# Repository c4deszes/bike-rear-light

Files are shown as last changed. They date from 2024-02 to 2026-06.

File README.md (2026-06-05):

# Rear Light

> An integrated tail, brake and turn signal light for bicycles.

## Gen 1

This generation is meant to demonstrate the tail light and brake light capabilities, turn signals
are not present.

The expected takeaways from it are:

- whether this simplified single PCB assembly is robust enough
- whether the amount of light produced is sufficient
- how certain lenses affect the optical qualities 
- what the thermals look like given the power consumption and enclosure with passive cooling
- whether this accelerometer is reliable to be used for the brake lights

Key findings:

- Accelerometer alone is not reliable for brake detection due to road vibrations. With filtering
  the reaction time goes up.
- Linear LED drivers are not efficient for the expected bus voltages, this is a problem for the
  continously on tail light
- Single LEDs spread out on a large area need lots of diffusing which reduces the light output

## Gen 1b

This generation is meant as a patch for the weak and uneven light output of Gen1. It's based on the
Gen1 front light hardware put inside a custom case.

There are no expectations.

Key findings:

- Mounting bracket broke during two incidents in an unservicable way

## Gen 2

This generation is meant to merge the good parts of Gen1 and Gen1b and improve a couple of things.
The main new feature is the included radar and the primary improvements are increased operational
voltage range and additional monitoring.

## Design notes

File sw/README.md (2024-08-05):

# Rear light software

## Open issues

- Scheduling automatic light diagnostic runs
- Fixing brake light error scenario determination
- Microcontroller temperature measurement and derating
- Accelerometer data processing and internal brake signal
- Diagnostic op. status and power status responses

## Deferred tasks

- Externally configurable product parameters (depends on diagnostic protocol extension)

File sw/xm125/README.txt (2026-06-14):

This package contains example source code, a makefile based build system, libraries, pre-built
binaries and documentation in order to start developing your own A121 radar applications
for the xm125 module.

Please see 'doc/XM125 Software User Guide.pdf' in order to get started with application development.

For more documentation please visit https://docs.acconeer.com/ or https://developer.acconeer.com

To view release notes use the following link: https://developer.acconeer.com/home/a121-docs-software/a121-sw-release-notes/

export GNU_INSTALL_ROOT=/opt/armgcc/arm-gnu-toolchain-14.2.rel1-x86_64-arm-none-eabi/bin/
export STM32CUBE_FW_L4_ROOT=/workspaces/xm125/STM32CubeL4/

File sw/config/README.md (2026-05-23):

# Board configurations

This folder includes board configurations for all released hardware versions.

Each board configuration must define the `bsp-config` interface target.
The target must have the following properties:
- Include folder
- BSP_IMU_DRIVER, defines the IMU driver to be used
- BSP_LED_DRIVER, defines the LED driver to be used

## IMU driver

Board configs currently can use `NONE` or `BMA456`. Whether the sensor is actually present is up
to the driver to detect.

## LED driver

Board configs currently can use `TLD2xxx`, `ILD8150`, `TLD509x` or `AL8891`.

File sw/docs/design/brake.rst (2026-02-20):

Brake component design
======================

The brake component is responsible for:

* Initializing the accelerometer
* Polling the accelerometer
* Determining braking condition based on the accelerometer data
* Determining braking condition based on signals coming from the RotorSensor peripheral

Initialization
--------------

The accelerometer is configured:

* Data rate: 100Hz
* Range: 2G
* Averaging: 4 samples (CIC)

If the sensor initialization fails for any reason the sensor is put into permanent failure state,
initialization will only be retried on a power-on-reset.

Operation
---------

During operation if the sensor initialized correctly then the acceleration data is polled and is
used by an algorithm to detect braking.

The internal signal is merged with the signal coming from the RotorSensor peripheral, if available,
to determine the overall braking condition. The brake signal status is forwarded to brightness control.

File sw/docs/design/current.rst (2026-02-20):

Current component design
========================

The current component is responsible for:

* Estimating the current used by the device
* Calculating the derating factor based on voltage and temperature

Initialization
--------------

* Current estimate is set to zero
* Derating factor is set to it's maximum

Operation
---------

* Current estimate is calculated based on the duty cycle and the battery voltage
* Derating factor is calculated based on the battery voltage and temperature
* If either the voltage or temperature is out of the valid range, the derating factor is set to maximum

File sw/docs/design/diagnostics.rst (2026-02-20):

Diagnostic components design
============================

Dianostic component is responsible for all diagnostic request handling, including:

* Software version reporting
* Operation status reporting
* Power status reporting
* Bootloader entry
* Idle and shutdown entry

Initialization
--------------

* Mode entry flags are cleared
* Operation status is set to ``init``

Operation
---------

* Operation status is updated, based on the light status
* Power status is updated, including voltage and current measurements

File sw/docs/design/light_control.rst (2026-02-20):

Light control component design
==============================

Light control is responsible for setting the PWM outputs according to the target duty cycle,
it's also responsible for detecting errors and diagnosing the output stages.

Initialization
--------------

The component sets up the TCC1 peripheral to output a 1kHz PWM signal with variable duty cycle.
The outputs are inverted because the drivers use an active low signal.

Initially PWM output is set to the maximum for the taillight this conforms to the hardware default state.

Operation
---------

Component is updated every 10ms, in this call:

* PWM duty cycle is reevaluated
* Output stage errors are detected
* Diagnosis requests are handled

Diagnosis (ILD8150)
-------------------

Diagnosis (TLD509x)
-------------------

Diagnosis (TLD2xxx)
-------------------

Tail light
~~~~~~~~~~

Tail light is evaluated segment by segment, initially all segments are off then the driver cycles
through them identifying the segments with short or open circuits. Afterwards if all segments are
good the status will be `ok`, if all segments are bad the status will be `error` otherwise the
status is `partial_error`.

Below is the timing diagram showing how each segment is individually enabled and the error pin
is sampled.

.. kroki::
    :type: wavedrom

    { signal: [
        { name: "!ERR",   wave: "x1314151x", data: ["S1", "S2", "S3"] },
        { name: "ENABLE", wave: "x0101010x" },
        { name: "!PWMI",  wave: "x10....1x" },
        { name: "INSET1", wave: "x010....x" },
        { name: "INSET2", wave: "x0..10..x" },
        { name: "INSET3", wave: "x0....10x" }
    ]}

Brake light
~~~~~~~~~~~

Brake light diagnosis is currently disabled.

.. kroki::
    :type: wavedrom

    { signal: [
        { name: "!ERR",   wave: "x131x", data: ["S1"] },
        { name: "ENABLE", wave: "x010x" },
        { name: "!PWMI",  wave: "x101x" },
        { name: "INSET",  wave: "x010x" },
    ]}

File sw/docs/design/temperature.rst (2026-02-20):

Temperature component design
============================

Temperature component is responsible for monitoring the temperature of the device
and updating the temperature status accordingly.

Initialization
--------------

The components sets up the microcontroller pin to read an external NTC.

Initially the temperature status is set to okay and the temperature is set to 25°C.

Operation
---------

* Temperature is measured
* Temperature status is updated, based on the temperature sensor reading

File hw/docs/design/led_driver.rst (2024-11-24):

LED driver design
=================

.. jupyter-execute::
    :hide-code:

    %config InlineBackend.figure_format = 'svg'
    import numpy as np
    from matplotlib import pyplot
    from IPython.display import Latex
    from UliEngineering.Electronics.Resistors import normalize_numeric

Challenges
----------

* Minimizing footprint and component number while including redundancy in the design
* Keeping the device efficient in a wide operating voltage range

Conclusions
-----------

* 2 channel drivers don't make sense if redundancy is important due to package size constraints
* To minimize footprint the optimal driver is either:

  * single channel and has boost capabilities (8 LEDs in a string, roughly Vf=16V)
  * quad channel and has buck capabilities (4x2 LED strings, roughly Vf=4V)

* Current source type drivers can only be used at low voltages, they would cutout if the string's
  forward voltage was too high

LED string design
-----------------

Given a nominal battery voltage of ``7.4V`` the longest LED string would be 3 LEDs with an average
forward voltage drop of ``2.5V``.

Brake & tail light
------------------

The chosen drivers are of the TLD2xxx series.

To achieve low power consumption the EN/DEN pin of the chip can be pulled low.

The driver is able to detect the following scenarios:

* Open load
* Short circuit
* Single LED short circuit

In case of open and shorted outputs the driver's reaction is determined by the D pin:

* When shorted to the ground the other channels will remain on
* When connected to a capacitor the capacitance determines the time after which channels are turned
  off

In case of a single LED short the DS pin does the same as the D pin but when it's shorted to ground
the output remains on with the shorted LED and with the capacitor it turns the channel off, the
capacitance in this case determines how often it tries to turn the channel on again.

The detection of single LED shorts is up to the proper sizing of the SLS resistor, when it's a short
to ground the feature is disabled, outputs will remain on.

In any of the above cases the ERROR pin is pulled low.

Detecting which channel has an error can be done by sampling the voltage on the INSET pins.

Configuration
~~~~~~~~~~~~~

* EN/DEN is pulled high to comply with the safety requirements,
  the microcontroller can then pull it low when lights are not needed.

* ERROR pin is connected to the microcontroller to report back errors.

* D/DS is shorted to ground, channels should remain on for as long as possible

* SLS is not used, as the variances in the forward voltage would not allow us to reliable detect
  this scenario.

* INSET is connected to transistors

Calculation
~~~~~~~~~~~

Calculation starts with determining the Input Set resistor value.

.. jupyter-execute::
    :hide-code:

    v_inset_ref = '1.22V'
    k = 300
    i_out = '20mA'

    r_inset = (k * normalize_numeric(v_inset_ref)) / normalize_numeric(i_out)

    Latex(f'R_{{INSETx}} = {r_inset:.03f}Ω')

The lights have to be operational in low voltage conditions, the lowest voltage devices should
expect is ``6.5V``. Since the device is a current source there's going to be a voltage drop across
it which then heats the device.

Signal light
------------

Turn indication is not implemented in Gen1, but here are few possible choices for it's driver:

* TLC6C5816-Q1 : 16 channel, on/off with group dimming?, no fault feedback, open drain, needs series resistor
* TLC6A598: 8 channel, on/off with dimming, no fault feedback
* TLC5917-Q1: 8 bit, shift register, prevents shorts
* TLC59208F: 8 bit, needs series resistor, i2c control with dimming per channel, no fault feedback
* TLC69601-Q1: 16 bit, i2c, fault detection, no further info, has many variants
* TPS92391: 6 channel, i2c, qfn32, boost/sepic with current sink
* LP8862-Q1: 2 channel, pwm (single channel), fault detection
* TPS92638-Q1: 8 channel, pwm (four channel), current source
* TLD7002-16ES: 16 channel, current source, fault detection, specifically for animations

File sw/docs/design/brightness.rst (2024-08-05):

Brightness component design
===========================

Brightness controller manages the target brightness for the LED segments.

Initialization
--------------

The controller starts in maximum brightness mode, in this mode it's actually the hardware
measures that enable maximum brightness.

Configuration
-------------

* Brightness curve: how the target brightness is mapped to the segments PWM control duty cycle.
* Standard minimum brightness: minimum brightness in daytime running mode
* Brake offset: target brightness increased when braking
* Strobe high/low offset: target brightness increased and decreased when strobing

Operation
---------

After initialization the controller follows the mode set by the system state manager.

* Off: all light elements are off
* Standard: following the brightness curve with an added minimum brightness, brake lights are enabled
* Adaptive: following the brightness curve, brake lights are enabled
* Emergency: fixed brightness and strobe mode
* Safety: fixed brightness and strobe mode
* Max: maximum brightness (hardware default)

Brightness curve
----------------

.. plot::

    import matplotlib.pyplot as plt
    import numpy as np
    cutoff_x = 100
    cutoff_y = 100
    max_x = 900
    max_y = 900
    min_level = 400
    emergency_level = 300
    safety_level = 800

    # Create the plot
    plt.figure(figsize=(10, 6))

    # Plot the cutoff and maximum points
    crossover_x = (min_level - cutoff_y) * (max_x - cutoff_x) / (max_y - cutoff_y) + cutoff_x
    plt.plot([0, cutoff_x, cutoff_x, max_x, 1000], [0, 0, cutoff_y, max_y, max_y], 'o-', color='green', label='Adaptive')
    plt.plot([0, crossover_x, max_x, 1000], [min_level, min_level, max_y, max_y], 'o-', color='blue', label='Standard')

    # Add horizontal lines for fixed brightness levels
    plt.axhline(y=emergency_level, color='orange', linestyle='--', label='Emergency')
    plt.axhline(y=safety_level, color='red', linestyle='--', label='Safety')

    # Add labels and title
    plt.xlabel('Target Brightness')
    plt.ylabel('PWM Duty Cycle')
    plt.title('Brightness to PWM Duty Cycle')
    plt.legend()

    # Show the plot
    plt.grid(True)
    plt.show()

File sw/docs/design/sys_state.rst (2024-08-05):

System state component design
=============================

System state manages the highest level states the rear light might have.

Initialization
--------------

The light starts in ``Init`` state, in this mode the lights are at maximum brightness.
The controller is not actually active in this case, rather hardware measures enable the
light by default.

Operation
---------

After initialization the light goes either into normal or safety mode.

* In normal mode the light uses the communicated target brightness, strobe mode and other settings.
* In safety mode the light uses the internally programmed fixed brightness and strobe mode.

The device transitions into safety mode if communication is lost for 4 seconds, with one exception
that is if the light has been instructed to use it's emergency brightness. This is a mode where the
system tries to save power and communication might be lost due to the battery draining.

The device may be put into idle and shutdown diagnostic modes.

* In idle mode the device instantly transitions to safety mode
* In shutdown mode the device goes into deep sleep, turning off all outputs

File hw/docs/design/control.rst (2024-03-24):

Controller
==========

The device uses the ATSAMD21E18A microcontroller, below are the pin assigments.

* Tail and brake light elements all have their separate IO, in future versions some pins could be
  made common (PWM, Enable)
* Accelerometer is used in SPI mode and both interrupt pins are connected, the number of pins used
  could be reduced by using I2C mode and not using interrupts

Pinout
------

.. list-table:: Pinout
    :header-rows: 1

    * - Pin
      - Pad
      - Peripheral
      - Function
      - Description

    * - PA00
      - 1
      - XTAL32
      - XIN32
      - 32kHz crystal input

    * - PA01
      - 2
      - XTAL32
      - XOUT32
      - 32kHz crystal output

    * - PA02
      - 3
      - EIC
      - EXTINT[2]
      - Tail light Error

    * - PA03
      - 4
      - EIC
      - EXTINT[3]
      - Brake light Error

    * - PA04
      - 5
      - TCC3
      - WO[2]
      - Tail light segment 3

    * - PA05
      - 6
      - TCC3
      - WO[3]
      - Tail light segment 2

    * - PA06
      - 7
      - TCC3
      - WO[4]
      - Tail light segment 1

    * - PA07
      - 8
      - TCC3
      - WO[5]
      - Brake light segment 1

    * - PA08
      - 11
      - GPIO
      - GPIO[8]
      - Tail light enable

    * - PA09
      - 12
      - GPIO
      - GPIO[9]
      - Brake light enable

    * - PA10
      - 13
      - TCC1
      - WO[0]
      - Tail light PWM control

    * - PA11
      - 14
      - TCC1
      - WO[1]
      - Brake light PWM control

    * - PA14
      - 15
      - EIC
      - EXTINT[14]
      - Accelerometer interrupt 2

    * - PA15
      - 16
      - EIC
      - EXTINT[15]
      - Accelerometer interrupt 1

    * - PA16
      - 17
      - SERCOM1
      - SERCOM PAD[0]
      - Accelerometer SPI Master In

    * - PA17
      - 18
      - SERCOM1
      - SERCOM PAD[1]
      - Accelerometer SPI Clock

    * - PA18
      - 19
      - SERCOM1
      - SERCOM PAD[2]
      - Accelerometer chip select

    * - PA19
      - 20
      - SERCOM1
      - SERCOM PAD[3]
      - Accelerometer SPI Master out

    * - PA22
      - 21
      - GPIO
      - GPIO[22]
      - LIN Transceiver Chip Select

    * - PA23
      - 22
      - GPIO
      - GPIO[23]
      - LIN Transceiver Transmit enable / Fault

    * - PA24
      - 23
      - SERCOM3
      - PAD2 (TX)
      - LIN Transceiver Transmit

    * - PA25
      - 24
      - SERCOM3
      - PAD3 (RX)
      - LIN Transceiver Receive

    * - PA30
      - 31
      - SWD
      - SWCLK
      - Serial-Wire-Debug clock

    * - PA31
      - 32
      - SWD
      - SWDIO
      - Serial-Wire-Debug data in/out

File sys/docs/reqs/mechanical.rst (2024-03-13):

Mechanical requirements
=======================

.. req-sys:: Seatpost mounting specification
    :id: SYS_REQ_ME_SEATPOST_SPEC
    :status: accepted, gen1.0
    
    The rear light shall be attachable to a seatpost with a diameter of ``31.6mm``.

.. req-sys:: Seatpost mounting mechanism
    :id: SYS_REQ_ME_SEATPOST_MOUNT
    :status: accepted
    :tags: security, safety, gen1.0

    The rear light shall not be detachable by hand, it should require some tool to make theft more
    difficult.

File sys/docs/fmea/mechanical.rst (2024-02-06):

Mechanical failure modes
========================

.. fmea:: Water ingress
    :id: FMEA_WATER_INGRESS
    :status: draft
    :probability: occasional
    :severity: critical
    :detection: low
    :mitigation: sealant

    Severity depends on the amount of water and the time the water has been in the system.
    Over time water corrodes parts, causes shorts or open circuits.

    The hardware should have mechanisms that indicate these shorts early and the software should
    report them back to the cycle computer as well as keeping track of them over time.

.. fmea:: Mount failure
    :id: FMEA_MOUNT_FAILURE
    :status: draft
    :probability: remote
    :severity: catastrophic
    :detection: high
    :mitigation: redundant mounting mechanism, cable tie down

    With the mount coming loose the rear light would slide down the seatpost, this is likely
    detected by the user.

    With the mount completely failing there's a risk of cable entanglement in the rear wheel.
    The cable therefore should be tied down at multiple points. The rear wheel being stuck would
    lead to an uncontrolled deceleration, the bike would likely be manuverable during it but the
    rear wheel would slip.

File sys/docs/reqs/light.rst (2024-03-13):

Light requirements
==================

Positioning and size
--------------------

.. req-sys:: Tail light position
    :id: SYS_REQ_TAIL_LIGHT_POSITION
    :status: draft
    :tags: legal, gen1.0

    The tail light shall be no more than 1.5m above ground level.

Tail light
----------

.. req-sys:: Tail light performance
    :id: SYS_REQ_TAIL_LIGHT_PERFORMANCE
    :status: draft
    :tags: legal, gen1.0

    The tail light shall be the color red, with a minimum brightness of 10 candela and a maximum
    brightness of 200 candela.

    The tail light shall be visible from 1.5km in good visibility conditions and 50m in poor
    visibility conditions.

.. req-sys:: Tail light modes
    :id: SYS_REQ_TAIL_LIGHT_MODES
    :status: draft
    :tags: legal, gen1.0

    The tail light shall be able to emit light continuously or blink at a rate of 60Hz.

Brake light
-----------

.. req-sys:: Brake light
    :id: SYS_REQ_BRAKE_LIGHT_PERFORMANCE
    :status: draft
    :tags: legal, safety, gen1.0

    The brake light shall be the color red, with a minimum brightness of 10 candela and a maximum
    brightness of 400 candela.

    The brake light shall turn on when the bicycle is decelerating with ``2.5 m/s^2`` and above.

Signal lights
-------------

.. req-sys:: Signal light performance
    :id: SYS_REQ_SIGNAL_LIGHT_PERFORMANCE
    :status: draft
    :tags: legal

    The signal lights shall be the color white-yellow, yellow, amber or orange, with a minimum
    brightness same as the tail light, the signal lights shall be clearly distinguishable from the
    tail light.

.. req-sys:: Signal light modes
    :id: SYS_REQ_SIGNAL_LIGHT_MODES
    :status: draft
    
    The signal lights shall be able to blink at a rate of 60Hz, the lights can also be sequentially
    animated, in this case all the lights need be to turned on before turning the anything off.

Light control
-------------

.. req-sys:: Light control
    :id: SYS_REQ_LIGHT_CONTROL
    :status: draft, gen1.0

    All light elements shall be synchronized in their switching frequency that's in the visible
    range (``120Hz - 1000Hz``).

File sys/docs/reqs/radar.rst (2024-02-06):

Radar requirements
==================

.. req-sys:: Radar minimum range
    :id: SYS_REQ_RADAR_MIN_RANGE
    :status: draft

    The radar shall detect targets up to 10m from it's mounting position.

.. req-sys:: Radar speed detection
    :id: SYS_REQ_RADAR_SPEED_RANGE
    :status: draft

    The radar shall have a relative speed detection capability of:

    * 5km/h for departing targets
    * 40km/h for approaching targets

.. req-sys:: Radar mounting
    :id: SYS_REQ_RADAR_MOUNTING
    :status: accepted

    The radar shall be mounted at a 3.5° offset to the left or have the sensitivity adjusted to
    focus on targets approaching from the left.

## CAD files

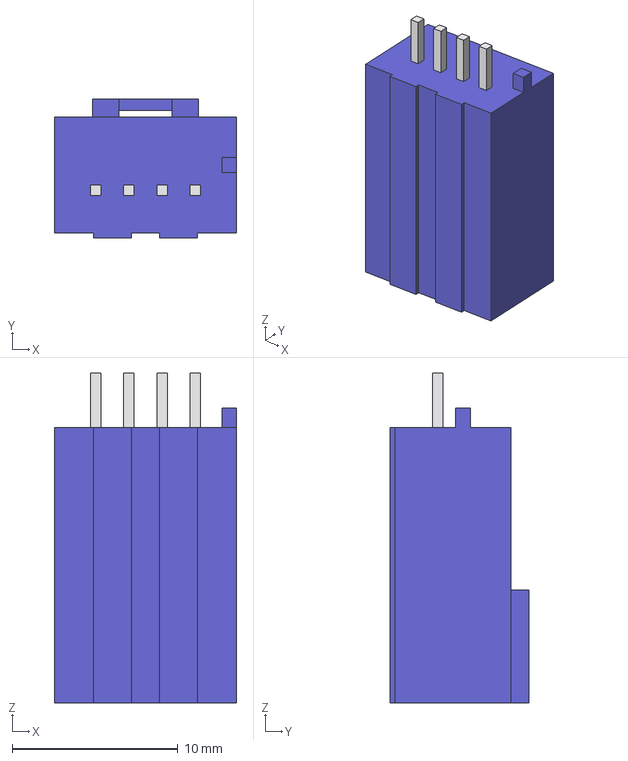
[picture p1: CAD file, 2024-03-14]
hw/design/models/B04B-JWPF-SK-R.step
11.0 x 8.40 x 19.9 mm

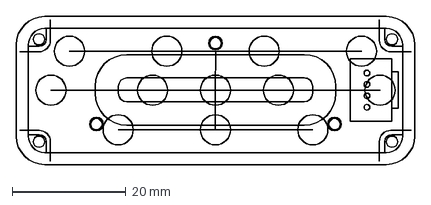
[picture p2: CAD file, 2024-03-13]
me/design/gen1.0/pcb_outline.dxf
70.0 x 26.0 mm

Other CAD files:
me/design/gen1.0/BrakeLight_v36.stl
me/design/gen1.0b/v5_MountingClamp.stl
me/design/gen1b/Lens.stl
me/design/gen1.0/Mount_v7.stl
me/design/gen1.0b/v23_Base_3pin.stl
me/design/gen1b/Seatpost_Clamp.stl
me/design/gen1.0b/v21_Lens.stl
me/design/gen1b/Seatpost_Mount.stl
me/design/gen1.0/TailLight_v36.stl
me/design/gen1.0b/v21_Cover.stl
me/design/gen1b/Base.stl
me/design/gen1.0/LightBlocker_v36.stl
me/design/gen1.0b/v5_Mounting.stl
me/design/gen1b/Cover.stl
me/design/gen1.0/Clamp_v7.stl
me/design/gen1.0b/v21_Base_4pin.stl
me/design/gen1.0/Case_v36.stl
me/design/gen1.0/Pcb_v36.stl

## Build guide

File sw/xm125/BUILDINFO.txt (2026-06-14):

The libraries in this package was built with the following configuration:

Compiler version:
    arm-none-eabi-gcc (Arm GNU Toolchain 13.3.Rel1 (Build arm-13.24)) 13.3.1 20240614 

Compiler flags:
    -mcpu=cortex-m4 -mthumb -mfloat-abi=hard -mfpu=fpv4-sp-d16 -DTARGET_ARCH_cm4 -DFLOAT_ABI_HARD
    -std=c99 -pedantic -Wall -Werror -Wextra -Wdouble-promotion -Wstrict-prototypes -Wcast-qual
    -Wmissing-prototypes -Winit-self -Wpointer-arith -Wshadow -MMD -MP -O2 -g -fno-math-errno
    -ffunction-sections -fdata-sections -flto=auto -ffat-lto-objects

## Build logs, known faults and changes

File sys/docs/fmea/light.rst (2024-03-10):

Light failure modes
===================

Tail light
----------

.. fmea:: Tail light failure
    :id: FMEA_TAIL_LIGHT_FAILURE
    :status: draft
    :probability: occasional
    :severity: catastrophic
    :detection: high
    :mitigation: multichannel layout

    Light failure could be caused by:

    * Shorted LEDs
    * Open LEDs
    * LED driver failure

    Mitigation should include hardware and software redundancy to ensure that the light doesn't
    turn off when it should be on.

    * Hardware should provide a default-on behavior, so the light is on even with certain software
      faults

    And obviously detection from hardware side should be maximized, should be able to detect shorts
    and opens, the rider may not detect the failure if it's not indicated by the cycle computer.

Brake light
-----------

.. fmea:: Brake light failure (off)
    :id: FMEA_BRAKE_LIGHT_FAILURE_OFF
    :status: draft
    :probability: occasional
    :severity: minor
    :detection: low
    :mitigation: increased hardware fault detection

    Light failure could be caused by:

    * Shorted LEDs
    * Open LEDs
    * LED driver failure

    Rider shall be notified in case of failure, but this failure is not severe as it's not a legal
    requirement to have working brake lights on bicycles.

.. fmea:: Brake light failure (on/switching)
    :id: FMEA_BRAKE_LIGHT_FAILURE_ON
    :status: draft
    :probability: occasional
    :severity: critical
    :detection: low
    :mitigation: software verification, protection of the control pins

    Failure could be caused by:

    * Software fault
    * Invalid data coming from the accelerometer
    * Short/open on the driver's control pins

    The mitigation should include:

    * Validation and filtering of the accelerometer data
    * Software limit on how often and how many times the brake light can turn on
    * Protection of the driver's control pins to ensure a default off behavior

    The brake light turning on when not actually braking can confuse the drivers behind.

Signal light
------------

.. fmea:: Signal light failure
    :id: FMEA_SIGNAL_LIGHT_FAILURE
    :status: draft
    :probability: occasional
    :severity: minor
    :detection: low
    :mitigation: increased hardware fault detection

    Light failure could be caused by:

    * Shorted LEDs
    * Open LEDs
    * LED driver failure

    Mitigation should include hardware and software fault detection.

    * Hardware should provide a default-off behavior, so the light is off even with software
      failures

    The rider may not detect the failure if it's not indicated by the cycle computer.
    One side blinking while the other cannot is fine, the rider should still be notified so they
    could revert back to using hand signals during turns.

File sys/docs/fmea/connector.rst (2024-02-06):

Connector failure modes
=======================

.. fmea:: Power pin failure
    :id: FMEA_POWER_PIN_FAILURE
    :status: draft
    :probability: occasional
    :severity: critical
    :detection: always
    :mitigation: none

    Power pin failure is usually caused by contact wear, the insulator being damaged or the
    connector coming loose.

    Detection needs to be done by the cycle computer, indicated by lack of communication or a
    short/open on the battery lines.

.. fmea:: Communication pin failure
    :id: FMEA_COMMUNICATION_PIN_FAILURE
    :status: draft
    :probability: occasional
    :severity: critical
    :detection: always
    :mitigation: safety on light mode

    Communication pin failure is usually caused by contact wear, the insulator being damaged or the
    connector coming loose.

    Detection needs to be done by the cycle computer, indicated by lack of communication. The ECU
    itself should also detect the lack of communication and set it's tail light to the set safety
    brightness, signal lights in this case should remain off. Brake light can keep working as long
    as the intertial data is available.

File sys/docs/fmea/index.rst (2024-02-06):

Failure mode analysis and evaluation
====================================

.. toctree::
    :glob:

    *

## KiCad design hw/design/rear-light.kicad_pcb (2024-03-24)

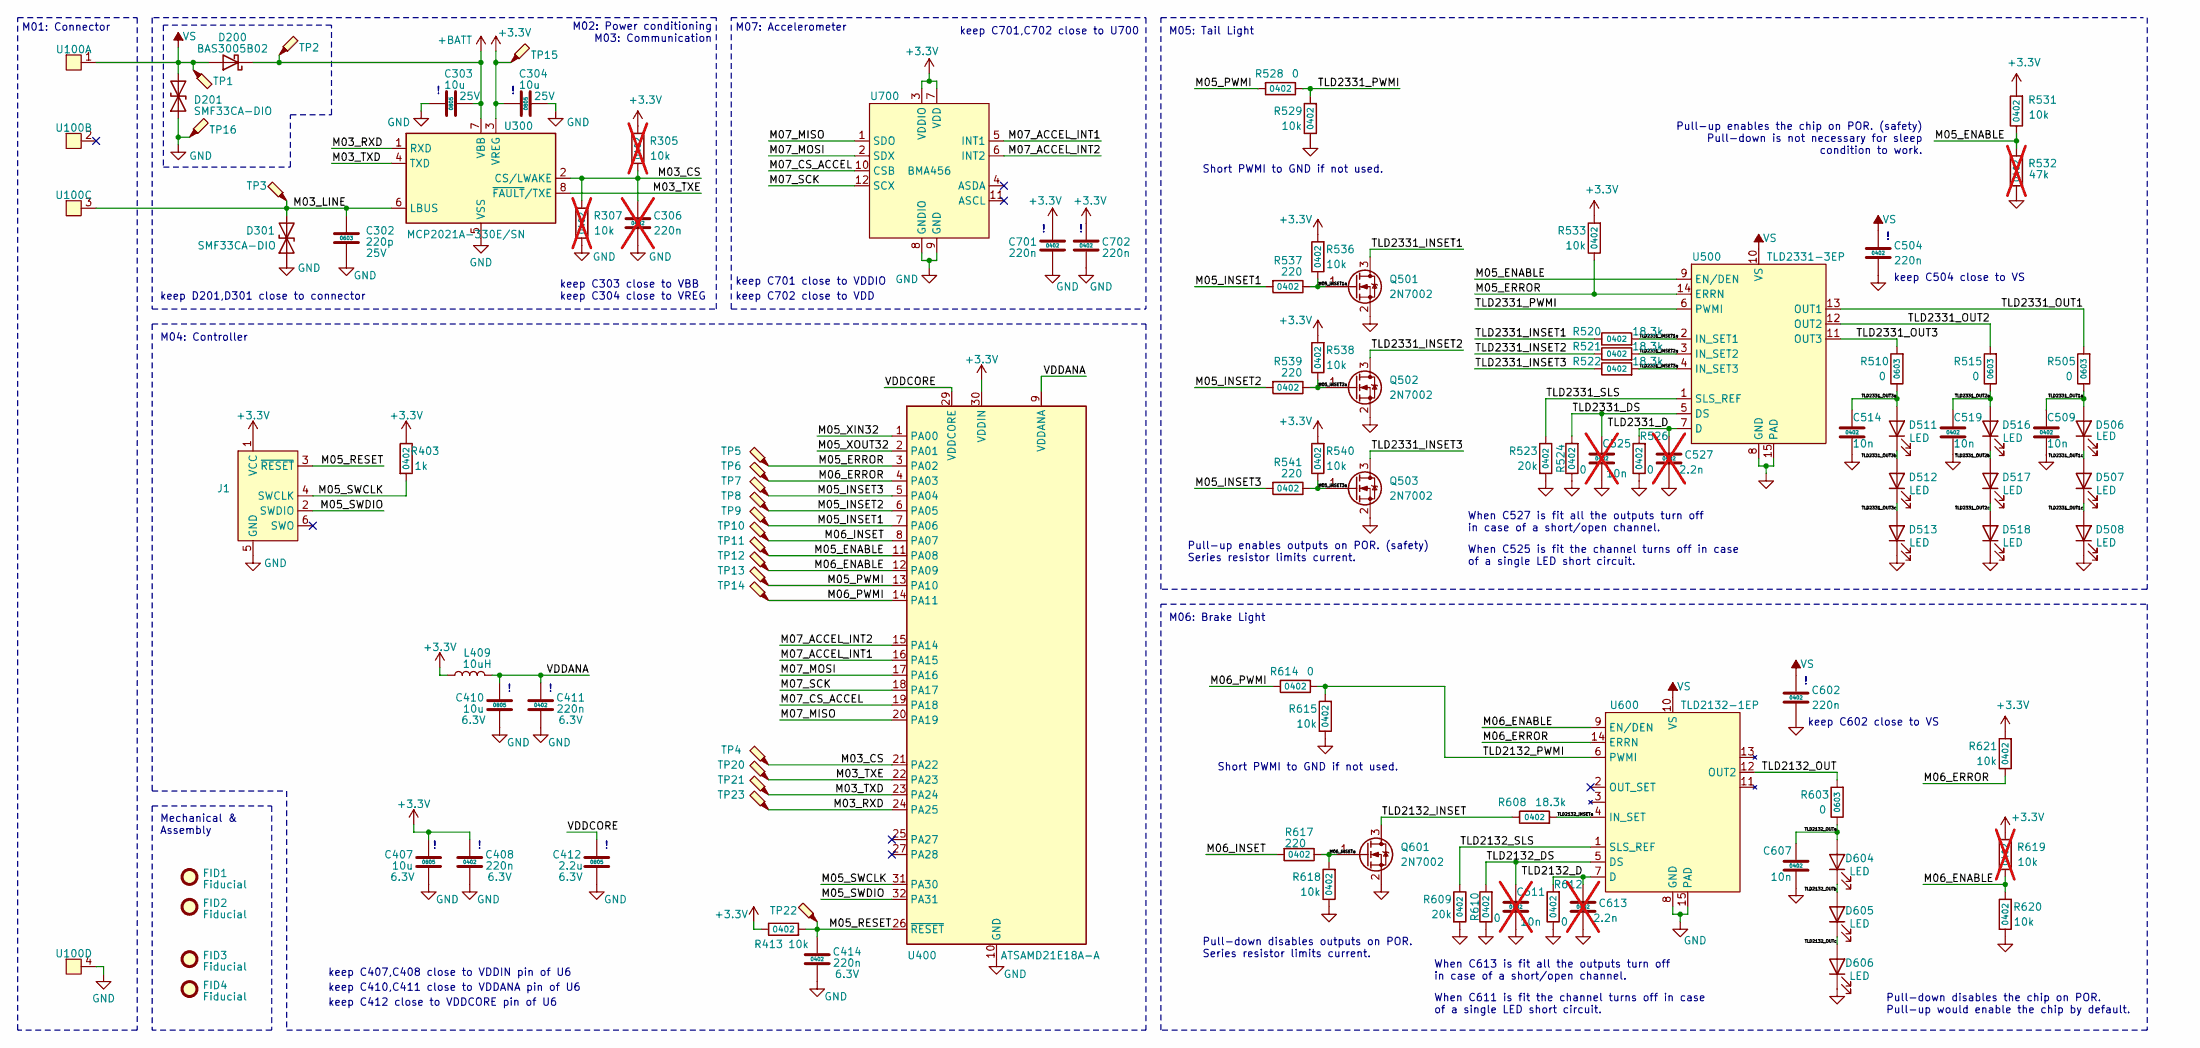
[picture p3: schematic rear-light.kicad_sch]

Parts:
C302: 220p; C_0603_1608Metric; Rating 25V
C303, C304: 10u; C_0805_2012Metric; Rating 25V
C306: 220n; C_0402_1005Metric; not fitted
C407, C410: 10u; C_0805_2012Metric; Rating 6.3V
C408, C411, C414: 220n; C_0402_1005Metric; Rating 6.3V
C412: 2.2u; C_0805_2012Metric; Rating 6.3V
C504, C602, C701, C702: 220n; C_0402_1005Metric
C509, C514, C519, C607: 10n; C_0402_1005Metric
C525, C611: 10n; C_0402_1005Metric; not fitted
C527, C613: 2.2n; C_0402_1005Metric; not fitted
D200: BAS3005B02; D_SOD-523
D201, D301: SMF33CA-DIO; D_SMF
D506, D507, D508, D511, D512, D513, D516, D517, D518, D604, D605, D606: LED; LED_0805_2012Metric
FID1, FID2, FID3, FID4: Fiducial; Fiducial_0.5mm_Mask1mm
J1: Conn_ARM_SWD_TagConnect_TC2030-NL; Tag-Connect_TC2030-IDC-NL_2x03_P1.27mm_Vertical
L409: 10uH; L_0805_2012Metric
Q501, Q502, Q503, Q601: 2N7002; SOT-23
R305, R307, R619: 10k; R_0402_1005Metric; not fitted
R403: 1k; R_0402_1005Metric
R413, R529, R531, R533, R536, R538, R540, R615, R618, R620, R621: 10k; R_0402_1005Metric
R505, R510, R515, R603: 0; R_0603_1608Metric
R520, R521, R522, R608: 18.3k; R_0402_1005Metric
R523, R609: 20k; R_0402_1005Metric
R524, R526, R528, R610, R612, R614: 0; R_0402_1005Metric
R532: 47k; R_0402_1005Metric; not fitted
R537, R539, R541, R617: 220; R_0402_1005Metric
TP1, TP2, TP3, TP4, TP5, TP6, TP7, TP8, TP9, TP10, TP11, TP12, TP13, TP14, TP15, TP16, TP20, TP21, TP22, TP23: TestPoint_Pad_1.0x1.0mm
U100: JST_JWPF_B04B-JWPF-SK-R_1x04_P2.00mm_Vertical
U300: MCP2021A-330E/SN; SOIC-8_3.9x4.9mm_P1.27mm
U400: ATSAMD21E18A-A; TQFP-32_7x7mm_P0.8mm
U500: TLD2331-3EP; Infineon_PG-TSDSO-14-22
U600: TLD2132-1EP; Infineon_PG-TSDSO-14-22
U700: BMA456; LGA-12_2x2mm_P0.5mm

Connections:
+3.3V: C304.1, C407.2, C408.2, C701.2, C702.1, J1.1 (VCC), L409.1, R305.1, R403.1, R413.1, R531.2, R533.2, R536.2, R538.2, R540.2, R619.2, R621.2, TP15.1, U300.3 (VREG), U400.30 (VDDIN), U700.3 (VDDIO), U700.7 (VDD)
+BATT: C303.2, D200.1 (K), TP2.1, U300.7 (VBB)
/M03_CS: C306.2, R305.2, R307.1, TP4.1, U300.2 (CS/LWAKE), U400.21 (PA22)
/M03_LINE: C302.1, D301.2 (A2), TP3.1, U100.3, U300.6 (LBUS)
/M03_RXD: TP23.1, U300.1 (RXD), U400.24 (PA25)
/M03_TXD: TP21.1, U300.4 (TXD), U400.23 (PA24)
/M03_TXE: TP20.1, U300.8 (~FAULT/TXE), U400.22 (PA23)
/M05_ENABLE: R531.1, R532.2, TP11.1, U400.11 (PA08), U500.9 (EN/DEN)
/M05_ERROR: R533.1, TP5.1, U400.3 (PA02), U500.14 (ERRN)
/M05_INSET1: R537.2, TP9.1, U400.7 (PA06)
/M05_INSET1a: Q501.1 (G), R536.1, R537.1
/M05_INSET2: R539.2, TP8.1, U400.6 (PA05)
/M05_INSET2a: Q502.1 (G), R538.1, R539.1
/M05_INSET3: R541.2, TP7.1, U400.5 (PA04)
/M05_INSET3a: Q503.1 (G), R540.1, R541.1
/M05_PWMI: R528.2, TP13.1, U400.13 (PA10)
/M05_RESET: C414.2, J1.3 (~RESET), R413.2, TP22.1, U400.26 (~RESET)
/M05_SWCLK: J1.4 (SWCLK), R403.2, U400.31 (PA30)
/M05_SWDIO: J1.2 (SWDIO), U400.32 (PA31)
/M05_XIN32: U400.1 (PA00)
/M05_XOUT32: U400.2 (PA01)
/M06_ENABLE: R619.1, R620.2, TP12.1, U400.12 (PA09), U600.9 (EN/DEN)
/M06_ERROR: R621.1, TP6.1, U400.4 (PA03), U600.14 (ERRN)
/M06_INSET: R617.2, TP10.1, U400.8 (PA07)
/M06_INSETa: Q601.1 (G), R617.1, R618.2
/M06_PWMI: R614.2, TP14.1, U400.14 (PA11)
/M07_ACCEL_INT1: U400.16 (PA15), U700.5 (INT1)
/M07_ACCEL_INT2: U400.15 (PA14), U700.6 (INT2)
/M07_CS_ACCEL: U400.19 (PA18), U700.10 (CSB)
/M07_MISO: U400.20 (PA19), U700.1 (SDO)
/M07_MOSI: U400.17 (PA16), U700.2 (SDX)
/M07_SCK: U400.18 (PA17), U700.12 (SCX)
/TLD2132_D: C613.2, R612.2, U600.7 (D)
/TLD2132_DS: C611.2, R610.2, U600.5 (DS)
/TLD2132_INSET: Q601.3 (D), R608.1
/TLD2132_INSETa: R608.2, U600.4 (IN_SET)
/TLD2132_OUT: R603.2, U600.12 (OUT2)
/TLD2132_OUTa: C607.2, D604.2 (A), R603.1
/TLD2132_OUTb: D604.1 (K), D605.2 (A)
/TLD2132_OUTc: D605.1 (K), D606.2 (A)
/TLD2132_PWMI: R614.1, R615.2, U600.6 (PWMI)
/TLD2132_SLS: R609.1, U600.1 (SLS_REF)
/TLD2331_D: C527.2, R526.2, U500.7 (D)
/TLD2331_DS: C525.2, R524.2, U500.5 (DS)
/TLD2331_INSET1: Q501.3 (D), R520.1
/TLD2331_INSET1a: R520.2, U500.2 (IN_SET1)
/TLD2331_INSET2: Q502.3 (D), R521.1
/TLD2331_INSET2a: R521.2, U500.3 (IN_SET2)
/TLD2331_INSET3: Q503.3 (D), R522.1
/TLD2331_INSET3a: R522.2, U500.4 (IN_SET3)
/TLD2331_OUT1: R505.2, U500.13 (OUT1)
/TLD2331_OUT1a: C509.2, D506.2 (A), R505.1
/TLD2331_OUT1c: D506.1 (K), D507.1 (K), D507.2 (A), D508.2 (A)
/TLD2331_OUT2: R515.2, U500.12 (OUT2)
/TLD2331_OUT2a: C519.2, D516.2 (A), R515.1
/TLD2331_OUT2b: D516.1 (K), D517.2 (A)
/TLD2331_OUT2c: D517.1 (K), D518.2 (A)
/TLD2331_OUT3: R510.2, U500.11 (OUT3)
/TLD2331_OUT3a: C514.2, D511.2 (A), R510.1
/TLD2331_OUT3b: D511.1 (K), D512.2 (A)
/TLD2331_OUT3c: D512.1 (K), D513.2 (A)
/TLD2331_PWMI: R528.1, R529.2, U500.6 (PWMI)
/TLD2331_SLS: R523.1, U500.1 (SLS_REF)
/VDDANA: C410.2, C411.2, L409.2, U400.9 (VDDANA)
/VDDCORE: C412.2, U400.29 (VDDCORE)
GND: C302.2, C303.1, C304.2, C306.1, C407.1, C408.1, C410.1, C411.1, C412.1, C414.1, C504.1, C509.1, C514.1, C519.1, C525.1, C527.1, C602.1, C607.1, C611.1, C613.1, C701.1, C702.2, D201.1 (A1), D301.1 (A1), D508.1 (K), D513.1 (K), D518.1 (K), D606.1 (K), J1.5 (GND), Q501.2 (S), Q502.2 (S), Q503.2 (S), Q601.2 (S), R307.2, R523.2, R524.1, R526.1, R529.1, R532.1, R609.2, R610.1, R612.1, R615.1, R618.1, R620.1, TP16.1, U100.4, U300.5 (VSS), U400.10 (GND), U400.28 (GND), U500.8 (GND), U500.15 (PAD), U600.8 (GND), U600.15 (PAD), U700.8 (GNDIO), U700.9 (GND)
VS: C504.2, C602.2, D200.2 (A), D201.2 (A2), TP1.1, U100.1, U500.10 (VS), U600.10 (VS)

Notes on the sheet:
keep C407,C408 close to VDDIN pin of U6
When C527 is fit all the outputs turn off in case of a short/open channel.
keep D201,D301 close to connector
Short PWMI to GND if not used.
Pull-up enables the chip on POR. (safety) Pull-down is not necessary for sleep condition to work.
M07: Accelerometer
When C613 is fit all the outputs turn off in case of a short/open channel.
M02: Power conditioning M03: Communication
keep C701,C702 close to U700
Mechanical & Assembly
keep C412 close to VDDCORE pin of U6
When C525 is fit the channel turns off in case of a single LED short circuit.
M05: Tail Light
When C611 is fit the channel turns off in case of a single LED short circuit.
keep C410,C411 close to VDDANA pin of U6
Pull-down disables the chip on POR. Pull-up would enable the chip by default.
keep C504 close to VS
keep C701 close to VDDIO
Pull-up enables outputs on POR. (safety) Series resistor limits current.
keep C702 close to VDD
Pull-down disables outputs on POR. Series resistor limits current.
M04: Controller
keep C602 close to VS
M01: Connector
keep C303 close to VBB keep C304 close to VREG
M06: Brake Light

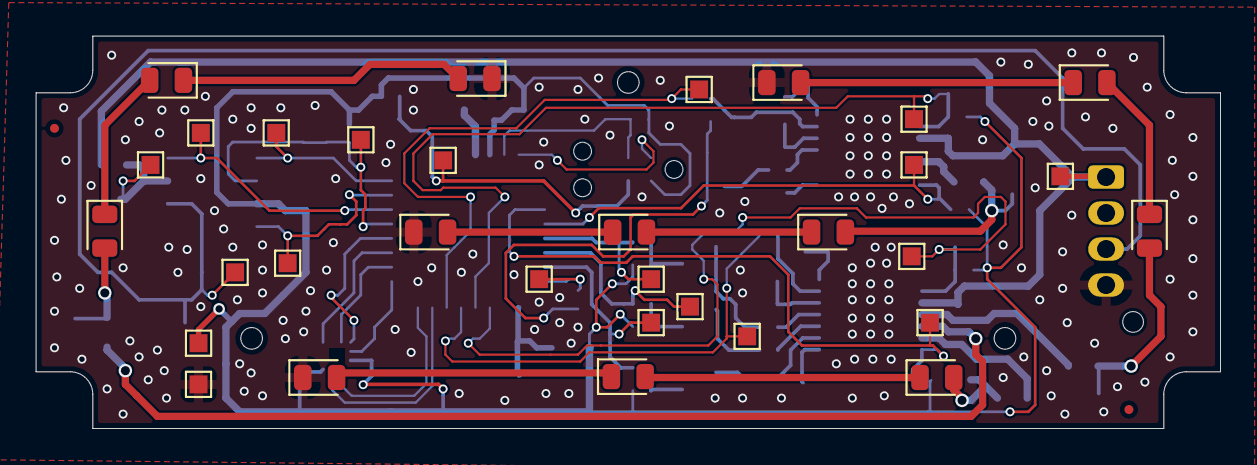
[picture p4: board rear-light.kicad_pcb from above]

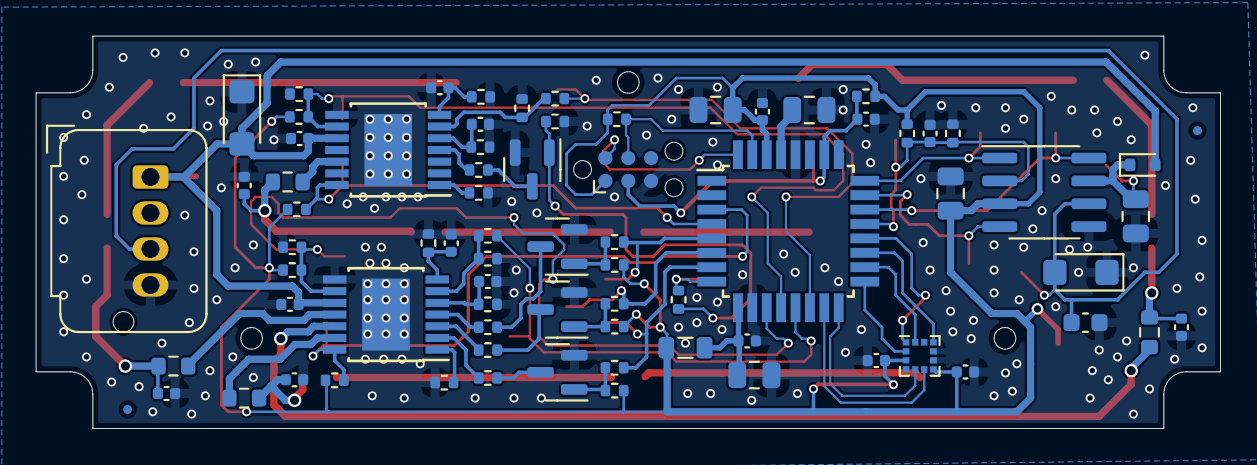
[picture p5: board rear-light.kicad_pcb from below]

Board: 2 copper layers, 65.8 x 21.8 mm, 109 parts (75 on the bottom side), 65 nets.

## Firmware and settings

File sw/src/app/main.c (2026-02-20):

#include <stddef.h>                     // Defines NULL
#include <stdbool.h>                    // Defines true
#include <stdlib.h>                     // Defines EXIT_FAILURE

#include "app/init.h"
#include "common/scheduler.h"

int main (void) {
    /* Initialize the application */
    APP_Init();

    /* Starts the scheduler */
    SCH_Enter();

    /* Execution should not come here during normal operation */
    return ( EXIT_FAILURE );
}

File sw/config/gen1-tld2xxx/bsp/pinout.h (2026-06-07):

#if !defined(BSP_PINOUT_H_)
#define BSP_PINOUT_H_

#include "hal/gpio.h"
#include "hal/sercom_usart.h"

// TODO: isn't great that we include it, since it could transitively end up in the app
#include "sam.h"

/** Tail light LED driver IC pins */
#define TLD2331_ENABLE_PORT PORT_GROUP_A
#define TLD2331_ENABLE_PIN 8

#define TLD2331_ERROR_PORT PORT_GROUP_A
#define TLD2331_ERROR_PIN 2

#define TLD2331_PWMI_PORT PORT_GROUP_A
#define TLD2331_PWMI_PIN 10
#define TLD2331_PWMI_PINMUX MUX_PA10E_TCC1_WO0
#define TLD2331_PWMI_WO 0

#define TLD2331_INSET1_PORT PORT_GROUP_A
#define TLD2331_INSET1_PIN 6

#define TLD2331_INSET2_PORT PORT_GROUP_A
#define TLD2331_INSET2_PIN 5

#define TLD2331_INSET3_PORT PORT_GROUP_A
#define TLD2331_INSET3_PIN 4

/** Brake light LED driver IC pins */
#define TLD2132_ENABLE_PORT PORT_GROUP_A
#define TLD2132_ENABLE_PIN 9

#define TLD2132_ERROR_PORT PORT_GROUP_A
#define TLD2132_ERROR_PIN 3

#define TLD2132_PWMI_PORT PORT_GROUP_A
#define TLD2132_PWMI_PIN 11
#define TLD2132_PWMI_PINMUX MUX_PA11E_TCC1_WO1
#define TLD2132_PWMI_WO 1

#define TLD2132_INSET1_PORT PORT_GROUP_A
#define TLD2132_INSET1_PIN 7

/** BMA456 3-axis accelerometer pins */
#define BMA456_SERCOM_INSTANCE SERCOM1

#define BMA456_ACC1_INT_PORT PORT_GROUP_A
#define BMA456_ACC1_INT_PIN 14

#define BMA456_ACC2_INT_PORT PORT_GROUP_A
#define BMA456_ACC2_INT_PIN 15

#define BMA456_SPI_MISO_PORT PORT_GROUP_A
#define BMA456_SPI_MISO_PIN 19
#define BMA456_SPI_MISO_PINMUX MUX_PA19C_SERCOM1_PAD3

#define BMA456_SPI_SCK_PORT PORT_GROUP_A
#define BMA456_SPI_SCK_PIN 17
#define BMA456_SPI_SCK_PINMUX MUX_PA17C_SERCOM1_PAD1

#define BMA456_SPI_CS_PORT PORT_GROUP_A
#define BMA456_SPI_CS_PIN 18

#define BMA456_SPI_MOSI_PORT PORT_GROUP_A
#define BMA456_SPI_MOSI_PIN 16
#define BMA456_SPI_MOSI_PINMUX MUX_PA16C_SERCOM1_PAD0

/** UART pins */
#define UART_SERCOM_INSTANCE SERCOM3

#define UART_RX_PORT PORT_GROUP_A
#define UART_RX_PIN 25
#define UART_RX_PINMUX MUX_PA25C_SERCOM3_PAD3

#define UART_TX_PORT PORT_GROUP_A
#define UART_TX_PIN 24
#define UART_TX_PINMUX MUX_PA24C_SERCOM3_PAD2

#define UART_CS_PORT PORT_GROUP_A
#define UART_CS_PIN 22

#define UART_TXE_PORT PORT_GROUP_A
#define UART_TXE_PIN 23

#define UART_TX_PAD SERCOM_USART_TX_PAD2
#define UART_RX_PAD SERCOM_USART_RX_PAD3

#endif // BSP_PINOUT_H_

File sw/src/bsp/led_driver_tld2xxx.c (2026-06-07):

#include "bsp/pinout.h"

#include "bsp/light_control.h"
#include "hal/tcc.h"
#include "common/swtimer.h"

#define LIGHT_DIAG_ENABLE_DURATION 10
#define LIGHT_DIAG_CHANNEL_DURATION 10
#define LIGHT_DIAG_POST_DURATION 10

static const gpio_pin_input_configuration input = {
    .pull = FLOATING,
    .sample = CONTINUOUS
};

static const gpio_pin_output_configuration output = {
    .drive = NORMAL,
    .input = false
};

static tcc_channel_setting_t pwm_channels[4];

typedef enum {
    lightcontrol_tail_diag_state_stopped,
    lightcontrol_tail_diag_state_enable,
    lightcontrol_tail_diag_state_in1,
    lightcontrol_tail_diag_state_in1_post,
    lightcontrol_tail_diag_state_in2,
    lightcontrol_tail_diag_state_in2_post,
    lightcontrol_tail_diag_state_in3,
    lightcontrol_tail_diag_state_in3_post
} lightcontrol_tail_diag_state_t;

typedef enum {
    lightcontrol_brake_diag_state_stopped,
    lightcontrol_brake_diag_state_enable,
    lightcontrol_brake_diag_state_in1,
    lightcontrol_brake_diag_state_in1_post
} lightcontrol_brake_diag_state_t;

static uint16_t tail_brightness;
static bool tail_diag_complete;
static uint8_t tail_segment_states;
static swtimer_t* taillight_diag_timer;
static lightcontrol_tail_diag_state_t taillight_diag_state;
static lightcontrol_feature_state_t taillight_state;

static uint16_t brake_brightness;
static bool brake_diag_complete;
static swtimer_t* brakelight_diag_timer;
static lightcontrol_brake_diag_state_t brakelight_diag_state;
static lightcontrol_feature_state_t brakelight_state;

static void TAILLIGHT_Init(void) {
    tail_brightness = LIGHTCONTROL_BRIGHTNESS_MAX;

    GPIO_PinWrite(TLD2331_ENABLE_PORT, TLD2331_ENABLE_PIN, HIGH);
    GPIO_SetupPinOutput(TLD2331_ENABLE_PORT, TLD2331_ENABLE_PIN, &output);

    GPIO_SetupPinInput(TLD2331_ERROR_PORT, TLD2331_ERROR_PIN, &input);

    /* PWM is Low active, by default enabling the taillight element */
    GPIO_PinWrite(TLD2331_PWMI_PORT, TLD2331_PWMI_PIN, LOW);
    GPIO_SetupPinOutput(TLD2331_PWMI_PORT, TLD2331_PWMI_PIN, &output);
    GPIO_EnableFunction(TLD2331_PWMI_PORT, TLD2331_PWMI_PIN, TLD2331_PWMI_PINMUX);

    GPIO_PinWrite(TLD2331_INSET1_PORT, TLD2331_INSET1_PIN, HIGH);
    GPIO_SetupPinOutput(TLD2331_INSET1_PORT, TLD2331_INSET1_PIN, &output);

    GPIO_PinWrite(TLD2331_INSET2_PORT, TLD2331_INSET2_PIN, HIGH);
    GPIO_SetupPinOutput(TLD2331_INSET2_PORT, TLD2331_INSET2_PIN, &output);

    GPIO_PinWrite(TLD2331_INSET3_PORT, TLD2331_INSET3_PIN, HIGH);
    GPIO_SetupPinOutput(TLD2331_INSET3_PORT, TLD2331_INSET3_PIN, &output);
}

static void BRAKELIGHT_Init(void) {
    brake_brightness = LIGHTCONTROL_BRIGHTNESS_MIN;

    GPIO_SetupPinOutput(TLD2132_ENABLE_PORT, TLD2132_ENABLE_PIN, &output);
    GPIO_PinWrite(TLD2132_ENABLE_PORT, TLD2132_ENABLE_PIN, LOW);

    GPIO_SetupPinInput(TLD2132_ERROR_PORT, TLD2132_ERROR_PIN, &input);

    /* PWM is low active, by default disabling the brakelight element */
    GPIO_PinWrite(TLD2132_PWMI_PORT, TLD2132_PWMI_PIN, HIGH);
    GPIO_SetupPinOutput(TLD2132_PWMI_PORT, TLD2132_PWMI_PIN, &output);
    GPIO_EnableFunction(TLD2132_PWMI_PORT, TLD2132_PWMI_PIN, TLD2132_PWMI_PINMUX);

    GPIO_PinWrite(TLD2132_INSET1_PORT, TLD2132_INSET1_PIN, HIGH);
    GPIO_SetupPinOutput(TLD2132_INSET1_PORT, TLD2132_INSET1_PIN, &output);
}

static void PWM_TIMER_Setup(void) {
    TCC_Reset(TCC1);

    pwm_channels[TLD2331_PWMI_WO].cc = LIGHTCONTROL_BRIGHTNESS_MAX;
    pwm_channels[TLD2331_PWMI_WO].drv_inv = true;
    pwm_channels[TLD2132_PWMI_WO].cc = LIGHTCONTROL_BRIGHTNESS_MIN;
    pwm_channels[TLD2132_PWMI_WO].drv_inv = true;

    TCC_SetupNormalPwm(TCC1, 999, pwm_channels);
    TCC_Enable(TCC1);
}

static void DIAG_Init(void) {
    tail_diag_complete = false;
    tail_segment_states = 0;
    taillight_diag_timer = SWTIMER_Create();
    taillight_diag_state = lightcontrol_tail_diag_state_stopped;
    taillight_state = lightcontrol_feature_state_ok;

    brake_diag_complete = false;
    brakelight_diag_timer = SWTIMER_Create();
    brakelight_diag_state = lightcontrol_brake_diag_state_stopped;
    brakelight_state = lightcontrol_feature_state_ok;
}

void LIGHTCONTROL_Init() {
    PWM_TIMER_Setup();

    TAILLIGHT_Init();
    BRAKELIGHT_Init();

    DIAG_Init();
}

void LIGHTCONTROL_SetBrightness(lightcontrol_segment_t feature, uint16_t brightness) {
    // TODO: clamp brightness, if needed disable PWM function and use high/low for 100% / 0%
    // TODO: check if PWM 0 and PWM 100% are achievable

    // TODO: might prefer this just being a setter function and doing the actual work in Update10ms
    if (feature == lightcontrol_segment_tail) {
        tail_brightness = brightness;
    }
    else if(feature == lightcontrol_segment_brake) {
        brake_brightness = brightness;
    }
}

uint16_t LIGHTCONTROL_GetBrightness(lightcontrol_segment_t feature) {
    if (feature == lightcontrol_segment_tail) {
        return tail_brightness;
    }
    else if(feature == lightcontrol_segment_brake) {
        return brake_brightness;
    }
    return LIGHTCONTROL_BRIGHTNESS_MIN;
}
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

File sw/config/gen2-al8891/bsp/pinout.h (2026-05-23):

#if !defined(BSP_PINOUT_H_)
#define BSP_PINOUT_H_

#include "hal/gpio.h"
#include "hal/sercom_usart.h"

// TODO: isn't great that we include it, since it could transitively end up in the app
#include "sam.h"

/** AL8891 LED driver IC pins */
#define AL8891_ENABLE_PORT PORT_GROUP_A
#define AL8891_ENABLE_PIN 0

#define AL8891_FAULT_PORT PORT_GROUP_A
#define AL8891_FAULT_PIN 1
#define AL8891_FAULT_PINMUX MUX_PA01A_EIC_EXTINT1

#define AL8891_ADIM_PORT PORT_GROUP_A
#define AL8891_ADIM_PIN 2
#define AL8891_ADIM_PINMUX MUX_PA02B_DAC_VOUT

#define AL8891_PDIM_PORT PORT_GROUP_A
#define AL8891_PDIM_PIN 3               // PDIM is GPIO only, TCC3 is not available on ATSAMD21E18A

#define AL8891_MON_PORT PORT_GROUP_A
#define AL8891_MON_PIN 4
#define AL8891_MON_PINMUX MUX_PA04B_ADC0_AIN4
#define AL8891_MON_ADC_INPUT ADC_INPUTCTRL_MUXPOS_PIN4_Val

/** Board NTC (Negative Temperature Coefficient) thermistor pins */
#define BOARD_NTC_PORT PORT_GROUP_A
#define BOARD_NTC_PIN 5
#define BOARD_NTC_PINMUX MUX_PA05B_ADC0_AIN5
#define BOARD_NTC_ADC_INPUT ADC_INPUTCTRL_MUXPOS_PIN5_Val

/** Board VBUS sense pins */
#define BOARD_VBUS_SENSE_PORT PORT_GROUP_A
#define BOARD_VBUS_SENSE_PIN 6
#define BOARD_VBUS_SENSE_PINMUX MUX_PA06B_ADC0_AIN6
#define BOARD_VBUS_SENSE_ADC_INPUT ADC_INPUTCTRL_MUXPOS_PIN6_Val

/** UART pins */
#define UART_SERCOM_INSTANCE SERCOM0

#define UART_CS_PORT PORT_GROUP_A
#define UART_CS_PIN 7

#define UART_TX_PORT PORT_GROUP_A
#define UART_TX_PIN 8
#define UART_TX_PINMUX MUX_PA08C_SERCOM0_PAD0

#define UART_RX_PORT PORT_GROUP_A
#define UART_RX_PIN 9
#define UART_RX_PINMUX MUX_PA09C_SERCOM0_PAD1

#define UART_TX_PAD SERCOM_USART_TX_PAD0
#define UART_RX_PAD SERCOM_USART_RX_PAD1

/** BMA456 3-axis accelerometer pins */
#define BMA456_SERCOM_INSTANCE SERCOM3

#define BMA456_SPI_MISO_PORT PORT_GROUP_A
#define BMA456_SPI_MISO_PIN 25
#define BMA456_SPI_MISO_PINMUX MUX_PA25C_SERCOM3_PAD3

#define BMA456_SPI_SCK_PORT PORT_GROUP_A
#define BMA456_SPI_SCK_PIN 23
#define BMA456_SPI_SCK_PINMUX MUX_PA23C_SERCOM3_PAD1

#define BMA456_SPI_CS_PORT PORT_GROUP_A
#define BMA456_SPI_CS_PIN 24

#define BMA456_SPI_MOSI_PORT PORT_GROUP_A
#define BMA456_SPI_MOSI_PIN 22
#define BMA456_SPI_MOSI_PINMUX MUX_PA22C_SERCOM3_PAD0

#define BMA456_INT1_PORT PORT_GROUP_A
#define BMA456_INT1_PIN 27
#define BMA456_INT1_PINMUX MUX_PA27A_EIC_EXTINT7

/** XM125 Radar pins */
#define XM125_SERCOM_INSTANCE SERCOM2
#define XM125_I2C_INSTANCE SERCOM1

#define XM125_RESET_PORT PORT_GROUP_A
#define XM125_RESET_PIN 10

#define XM125_WAKE_PORT PORT_GROUP_A
#define XM125_WAKE_PIN 11

#define XM125_TX_PORT PORT_GROUP_A
#define XM125_TX_PIN 14
#define XM125_TX_PINMUX MUX_PA14C_SERCOM2_PAD2
#define XM125_TX_PAD SERCOM_USART_TX_PAD2

#define XM125_RX_PORT PORT_GROUP_A
#define XM125_RX_PIN 15
#define XM125_RX_PINMUX MUX_PA15C_SERCOM2_PAD3
#define XM125_RX_PAD SERCOM_USART_RX_PAD3

#define XM125_SDA_PORT PORT_GROUP_A
#define XM125_SDA_PIN 16
#define XM125_SDA_PINMUX MUX_PA16C_SERCOM1_PAD0

#define XM125_SCL_PORT PORT_GROUP_A
#define XM125_SCL_PIN 17
#define XM125_SCL_PINMUX MUX_PA17C_SERCOM1_PAD1

#define XM125_INT_PORT PORT_GROUP_A
#define XM125_INT_PIN 18
#define XM125_INT_PINMUX MUX_PA18A_EIC_EXTINT2

#define XM125_BOOT_PORT PORT_GROUP_A
#define XM125_BOOT_PIN 19

#define XM125_GPIO0_PORT PORT_GROUP_A
#define XM125_GPIO0_PIN 28


#endif // BSP_PINOUT_H_

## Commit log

2024-03-13 Mechanical design Gen1.0
    [BrakeLight_v36.stl, Case_v36.stl, Clamp_v7.stl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]
2024-03-14 Hardware design Gen1.0
    [B04B-JWPF-SK-R.step, rear-light.kicad_pcb, rear-light.kicad_sch]
2024-03-24 Gen1.0 design finalization (#1)
    * Final layout for Gen1.0, PCB has been ordered
    * Design documentation is mostly done
    * Schematic has been completed
    [rear-light.kicad_pcb, rear-light.kicad_sch]
2024-08-05 Gen1.0 Initial software (#2)
    * Software blinks brake and tail lights
    * System and brightness controller
    * Safety blinking mode
    * Rapid strobe and strobe interface rework
    * Working accelerometer data polling
    * Working signal handling
    * System state transitions are working
    * Boot request support
    * Reacts to external brake signal
    * Updated UART and SPI drivers
    * Debug signals
    * Working diagnostic runs
    * New brightness settings
    * Software design documentation
    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
    [factory-flash.cfg, flash.cfg]
2024-08-19 Working light control
    [flash.cfg]
2024-08-30 Pin UDS version
2024-10-14 Gen1b mechanical parts
    [Base.stl, Cover.stl, Lens.stl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]
2024-11-24 Bootloader and HAL update (#3)
    * New bootloader and HAL integration
    * Internal brake signal (disabled)
    * Updates electronics system version
2024-11-24 Uploading datasheets (#4)
    Changes 220n capacitors to 100n
    PWMI pull downs populated according to expected default behavior
    [rear-light.kicad_sch]
2025-10-22 Gen1.0b mechanical design (#5)
    This is a design based on front light gen1.0 hardware, includes
    a mount.
    [v21_Base_4pin.stl, v21_Cover.stl, v21_Lens.stl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]
2026-02-10 Restructuring components
    Fixes schedule timer not having power
    Fixes missing transition from safety to normal mode
    Reintroduced braking component, sensor can be disabled
    Accelerometer is initialized at board level
    LINE protocol interface pushed down to board level to aid SIL
    Updating LINE and UDS libs to latest version
    Reenabling bootloader entry function
    [accel_bma456.c, board.c, led_driver_tld509x.c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]
2026-02-20 Big rework
    INIT: changed loading sequence
    TASKS: changed task allocation
    VOLT: draft of voltage measurement
    SYSSTATE: config loading
    TEMP: draft of temperature measurement
    CURRENT: draft of current estimator
    DIAG: new component handling diag functions
    COMM: Moved diagnostic functions into DIAG
    BRIGHTNESS: Config loading interface
    BRAKE: interfaces for debug signals
    USART: consistent function names, reuse HAL GPIO config
    [accel_bma456.c, board.c, led_driver_tld509x.c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]
2026-02-24 Working TTADC, support for all 3 board versions
2026-02-27 Updated lightcontrol interface and TLD509x driver
2026-02-27 Fixes analog modulation at 0 brightness Fixes PWM modulation build
    [led_driver_tld509x.c, pinout.h]
2026-05-24 Calibration, wake manager, systick
2026-06-07 Compiling all board variants
2026-06-08 New default config for each board Calibration can be saved
2026-06-20 Devcontainer includes STM32 dev pack
2026-06-21 Fix calibration saving
2026-06-21 Disabling emergency entry at low voltage
2026-06-21 Fix for Gen1x not having Uart interrupt handler
    [usart.c]
